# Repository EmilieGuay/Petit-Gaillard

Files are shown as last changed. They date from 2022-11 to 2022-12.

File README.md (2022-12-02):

# Petit Gaillard

Le Petit Gaillard est un robot assez simple à préparer et à programmer. Il possède deux bras qui peuvent bouger grâce à 4 servomoteurs positionnels. 

On peut donc lui faire prendre des postures ou encore le faire danser!

Idéal pour apprendre la programmation des servomoteurs positionnels et aussi très amusant :).

## Programmation

On peut programmer les servomoteurs positionnels pour que leur arbre soit à une position angulaire donnée. Le moteur se positionnera à cet angle et y restera. Les servomoteurs utilisés peuvent généralement couvrir des angles de 0 à 180 degrés. 

Pour des suggestions d'activités à faire avec le Petit Gaillard, voir les documents dans le dossier "Programmation". 

La première activité se nomme "Petit Gaillard", il existe 3 versions, en fonction de l'application utilisée pour programmer le Petit Gaillard, soit mBlock, Blockly ou Arduino IDE. Les feuiles de postures supplémentaires et le défi ultime peuvent être utiles ici. 

Pour une utilisation du Petit Gaillard avec un modèle d'intelligence artificielle (classification d'images, de sons ou de postures), consulter le répertoire "App-IA" (www.github.com/EmilieGuay/App-IA). 

La deuxième activité se nomme "Faire danser le Petit Gaillard".

## Matériel et préparation

### Impression 3D

Les fichiers fournis sont en format ".stl". Il est possible de les ouvrir dans un logiciel d'impression 3D pour les péparer pour l'impression. 
Pour obtenir des formats de fichiers modifiables, contactez-moi. 

À noter : les deux bras sont identiques, de même que les deux avant-bras.

Il est possible que les formes doivent être tournées pour permettre une meilleure impression. Le haut, par exemple, devrait se trouver la face contre la surface d'impression et non pas debout. Pour les bras et les avant-bras, il est mieux de les mettre à plat, avec la face comprenant l'emplacement pour le bras/embout/corne pour le servomoteur vers le haut.

Les pièces n'ont pas besoin d'une grande précision. Généralement, 0.28 mm comme épaisseur de couche devrait convenir, mais il pourrait être utile de choisir plus petit (0.20mm ou 0.16 mm) pour les bras et les avant-bras. Une densité de remplissage autour de 15 % devrait convenir.

Le haut entre directement dans le bas. Les deux pièces devraient s'emboîter assez bien pour ne pas avoir besoin de fixation supplémentaire. Il faut parfois sable un peu le haut pour qu'il soit facile à placer dans le bas

### Version "bricolage à la maison"

Pour ceux qui souhaiteraient faire leur porpre Petit Gaillard, mais qui n'ont pas d'imprimante 3D, il est aussi possible d'en fabriquer un en carton. Pour de meilleurs résultats, utiliser un carte très rigide pour le corps, les bras et les avant-bras. Pour la base du robot, il faudra voir ce qui est disponible à la maison. On peut, par exemple, se servir d'une boîte de céréales vide. Il faudra peut-être renforcer certaines parties. La base de la boîte peut servir de base au robot. et on découpe le coprs et la base d'une seule pièce dans la boîte. 

Il est important que le matériel pour faire les bras et les avant-bras soit léger car les servomoteurs suggérés (format micro) ne sont pas conçus pour lever des grandes charges. 

Le fichier "Dimensions.pdf" peut aider dans la planification, mais c'est aussi une bonne opportunité de laisser aller son imagination.

Pour fixer les servomoteurs et leurs attaches sur le robot, la colle chaude et le ruban adhésif sont assez efficaces. 

### Choix des servomoteurs

Vous devez utiliser des servomoteurs positionnels pour réaliser le Petit Gaillard. Acheter ceux dont les fils se trouvent à la base, et non sur le côté. Sinon, il risque d'être difficile de les installer sur les bras ou le haut du robot. Si on installe les servomoteurs différemment que la méthode proposée, il risque de ne pas y avoir assez d'espace pour que les bras puissent bouger.  Pour plus d'informations, voir le document "Matériel et préparation du Petit Gaillard.pdf". Vous pouvez aussi consulter le vidéo sur le Petit Gaillard. 

De préférence, choisir des servomoteurs qui permettent une alimentation entre 4.8V à 6V.

## Vidéos

à venir

Des activités supplémentaires seront ajoutées avec le temps

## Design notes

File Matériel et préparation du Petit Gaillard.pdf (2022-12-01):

### 1. Introduction

Le Petit Gaillard est un robot simple qui est une bonne introduction à la programmation des robots et à l’utilisation des servomoteurs positionnels. Il possède deux bras qui peuvent bouger grâce à un servomoteur dans l’épaule et un autre dans le coude.

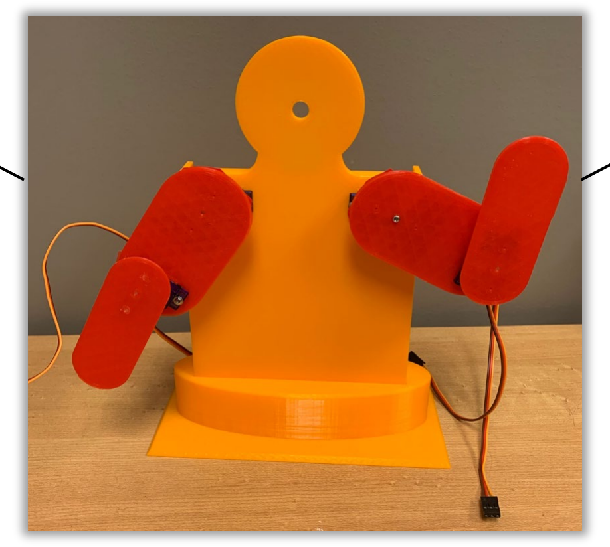
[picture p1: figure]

On peut donc le faire prendre des poses en particulier ou encore le faire danser !

Le présent document présente les pièces formant le Petit Gaillard et la façon de l’assembler au départ.

Attention : dans le présent document et les autres documents préparer, la gauche et la droite du robot sont définie comme sur la figure suivante. Il s’agit de votre gauche ou votre droite, comme si le robot était votre image dans le miroir.

# Matériel d’un kit du Petit Gaillard et préparation

## Club de robotique

### CÉGEP DE JONQUIÈRE

Droite du
robot

Gauche du
robot

2

### 2. Matériel

- 1 carte Arduino
- 1 fils USB-B vers USB-A long
- 4 x 3 fils mâle-mâle
- 4x 3 fils mâle-femelle
- 4 servomoteurs positionnels format micro dont les fils sortent vers le bas du servomoteur et non le côté. De préférence permettant des tensions entre 4.8 V et 6V.
- 1 platine d’essai moyenne

Impression 3D :
- 1 dessous du robot
- 1 corps du robot
- 2 bras
- 2 avant-bras

Alimentation recommandée :
- 1 support de pile 4xAA
- 4 piles AA (peuvent être rechargeables)

Autre alimentation possible :
- 1 blindage Gravity: IO Expansion Shield for Arduino V7.1 de DFRobot

Pour l’installation des servomoteurs :
- 1 petit tournevis cruciforme
- 1 fusil à colle chaude ou ruban adhésif de type électrique

### 3. Assemblage

### Les avant-bras

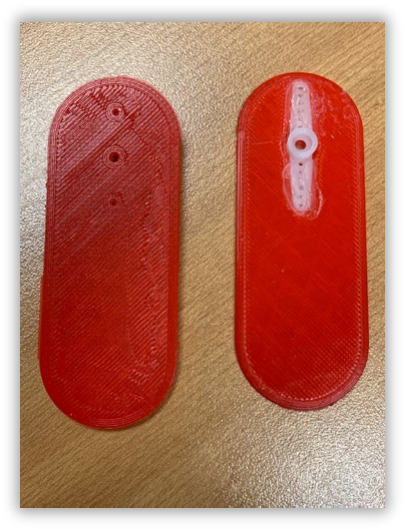
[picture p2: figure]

Les deux avant-bras sont identiques. Il suffit de fixer les attaches pour servomoteurs (en général, elles viennent avec les servomoteurs quand on les achète) dans l’emplacement prévu à cette fin sur la pièce imprimées 3D. On peut la fixer avec de la colle chaude ou autre type de colle (la colle en bâton ne fonctionne pas à cette fin) ou un ruban adhésif électrique (isolant) ou autre. On peut aussi utiliser des petites vis qui sont fournies avec le servomoteur, mais ce n’est pas idéal car elles devraient être utilisées principalement pour fixer les servomoteurs eux-mêmes.

3

Si du ruban adhésif est utilisé, il peut arriver que l’attache du servomoteur se détache de l’avant-bras, mais il faut simplement la fixer à nouveau.

Note : il est possible que l’attache du servomoteur n’entre pas bien dans l’emplacement prévu à cette fin sur l’avant-bras. Le format des attaches varie d’un fabriquant à l’autre, alors il est difficile d’avoir toujours le bon format. Il est toujours possible de modifier l’attache ou de la fixer malgré tout.

### Les bras

Il faut fixer les servomoteurs sur les bras de la façon suivante :

## Bras gauche Bras droit

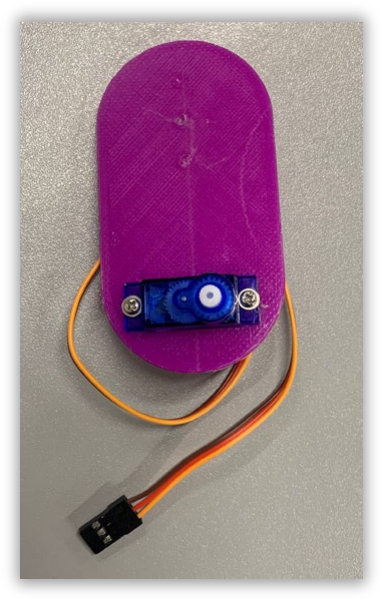
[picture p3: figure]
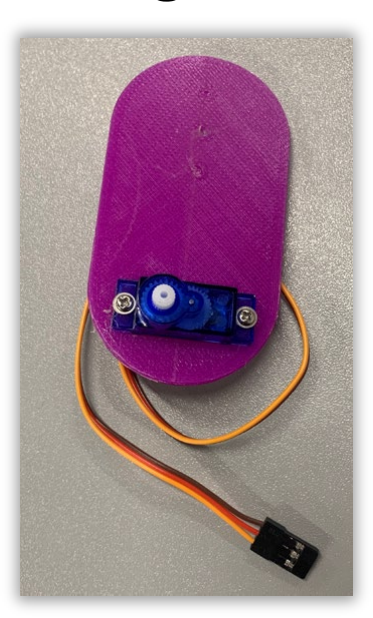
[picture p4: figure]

La face qui est vue ici est la face de devant. Il faut utiliser des vis pour fixer les servomoteurs, ou encore de la colle chaude. Les deux moteurs n’ont pas la même orientation dans les deux cas. Le but est de mettre le fil du servomoteur vers l’extérieur.

Les vis utilisées sont celles qui viennent avec les servomoteurs. Il peut arriver qu’elles dépassent à l’arrière du bras. Il est toujours possible de mettre un peu de colle chaude ou autre chose sur la pointe de la vis qui dépasse pour éviter de se piquer dessus.

Il faut aussi installer une attache pour les servomoteurs sur la face arrière. Procéder comme avec les avant-bras.

La raison pour laquelle il faut absolument que les fils du servomoteur sortent dans le bas de celui-ci est pour pouvoir les installer comme il le faut.

4

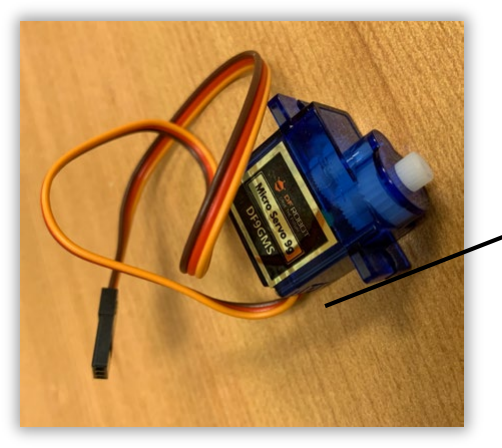
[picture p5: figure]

En effet, si les fils sortent sur le côté, il sera difficile de glisser le servomoteur dans l’ouverture pour qu’il soit ainsi :

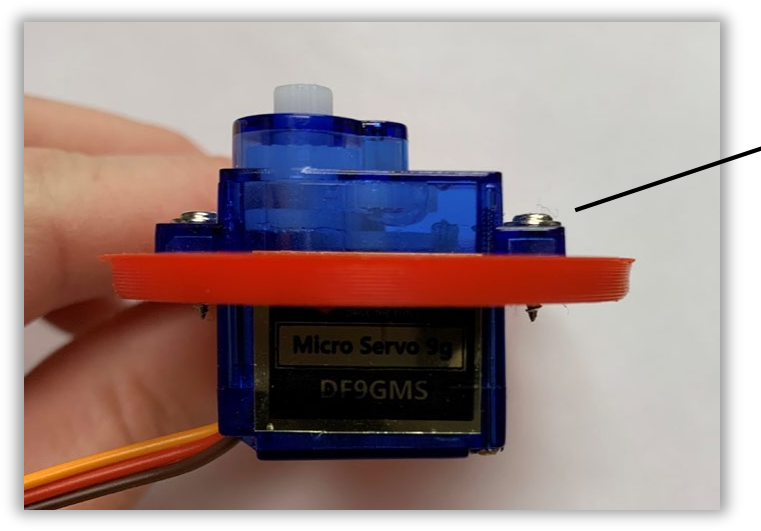
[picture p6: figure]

Sinon, il risque de manquer d’espace pour le que servomoteur du bars puisse passer entre le bras et le corps.

Fil sortant dans
le bas du
servomoteur

Partie plus
large de ce
côté

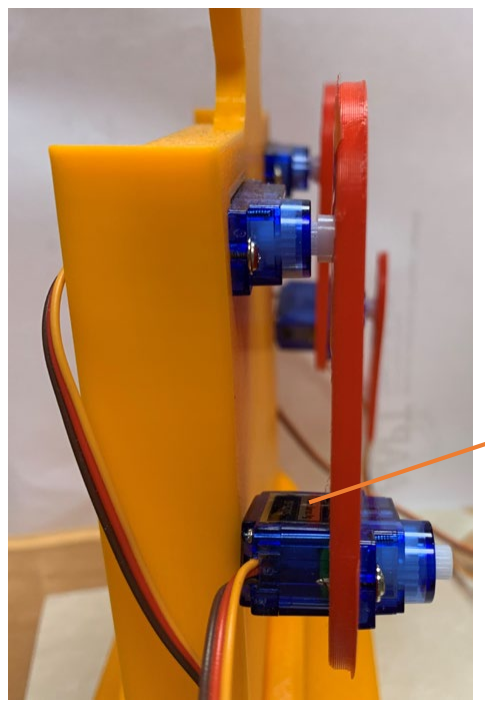
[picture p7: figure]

Espace entre
le bras et le
corps

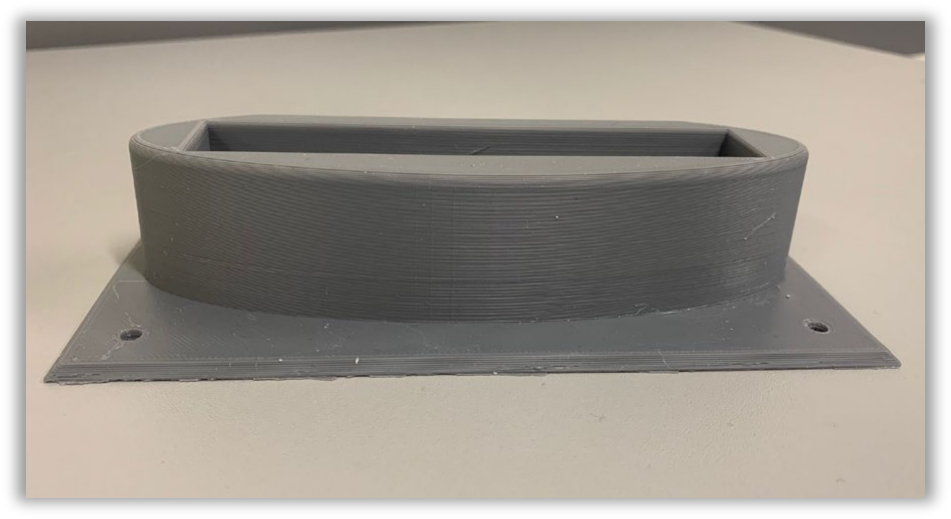
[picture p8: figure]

5

### Le corps du Petit Gaillard

Pour finir la préparation du corps du Petit Gaillard, il suffit de fixer deux servomoteurs dans les ouvertures des épaules. Il faut procéder comme dans le cas des bras, avec la même orientation.

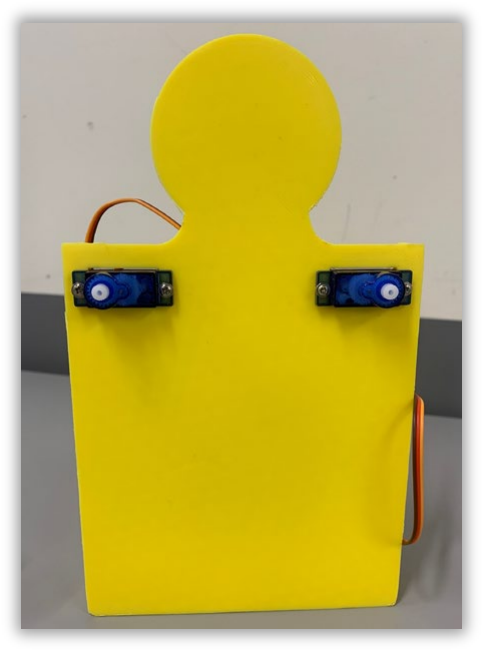
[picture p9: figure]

### Le dessous du Petit Gaillard

Aucune préparation n’est nécessaire !

### Assemblage final :

Placer le corps dans l’ouverture du bas du robot sans autre besoin de fixation. Au besoin, limer un peu la base du corps s’il est difficile de le faire entrer.

Il est préférable de ne pas placer les bras et les avant-bras sur le robot au départ, car on ignore la position des servomoteurs. Pour savoir comment les placer, suivre les instructions du document « Petit Gaillard mBlock.pdf », « Petit Gaillard Blockly.pdf » ou « Petit Gaillard Arduino.pdf ».

### 4. Circuit et alimentation :

Il reste à brancher les servomoteurs dans l’alimentation et la carte Arduino.

Important : Il est mieux les branchements sont faits derrière le Petit Gaillard pour que les fils soient derrière celui-ci.

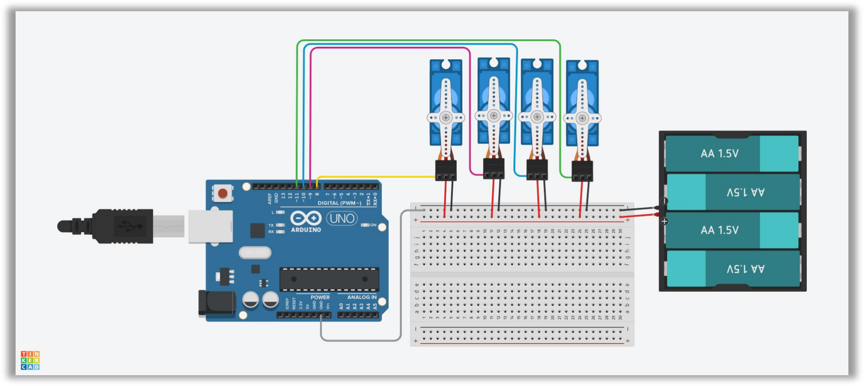
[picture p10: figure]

6

Dans les deux cas, il est recommandé de brancher les fils de signal (fil orange du servomoteur) dans les broches digitales suivantes de la carte Arduino :

Servomoteur | Broche
Épaule Gauche | 8
Épaule Droite | 9
Coude Gauche | 10
Coude Droit | 11

Les autres broches fonctionneraient aussi, mais cela suit ce qui est fait dans les documents d’activités proposées avec le Petit Gaillard. Si on choisit d’autres broches, il faut en tenir compte lors de la programmation.

Alimentation recommandée :

Il est toujours préférable de séparer l’alimentation électrique des moteurs et celle de l’électronique. Parfois, on réussit à le faire avec un circuit, mais on peut aussi utiliser deux sources de courant/tension. Ici, la carte Arduino est alimentée par l’ordinateur via le fil USB et le bloc de 4 piles alimente les servomoteurs.

Il est très important de ne pas oublier de brancher une broche GND de la carte de type Arduino avec la borne négative (« - ») du bloc de piles.

Note : On choisit les piles de telle sorte que l’on respecte la tension recommandée par le fabricant. Certains servomoteurs supportent une tension entre 4.8 V et 6 V, ce qui est parfait avec un bloc de 4 piles AA, rechargeables (4.8 V) ou non (6 V). ON pourrait aussi utiliser des piles AAA si le support de 4 piles utilise ce format.

7

Alimentation alternative 1 :

On peut utiliser la broche +5V comme alimentation pour les servomoteurs. Cependant, il faut s’assurer que les servomoteurs ne restent pas coincés. Ce n’est pas la méthode idéale.

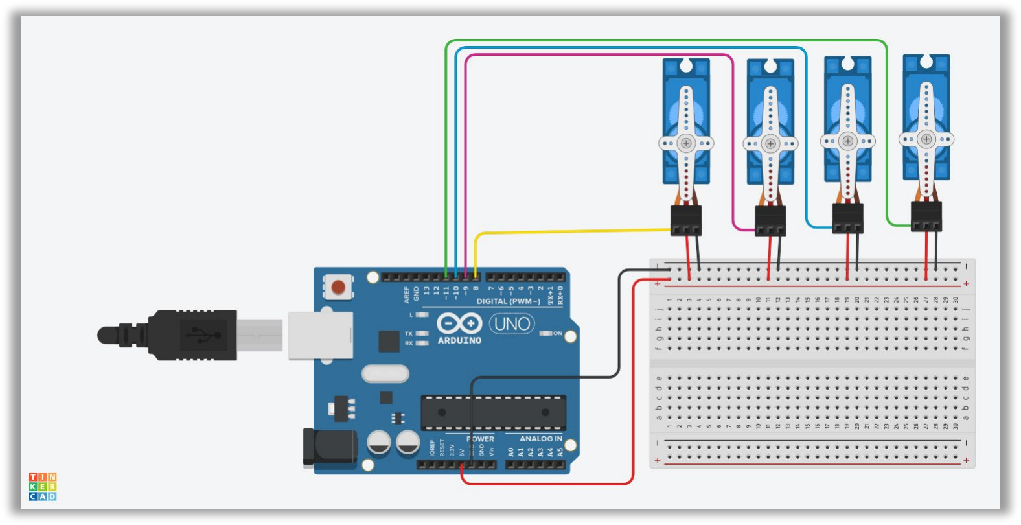
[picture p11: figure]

Il peut arriver que cela demande trop de courant via le port USB et que l’ordinateur déconnecte la carte Arduino.

Autre version alternative

On peut aussi utiliser un blindage (« Shield »), par exemple le Gravity: IO Expansion Shield for Arduino V7.1 de DFRobot.

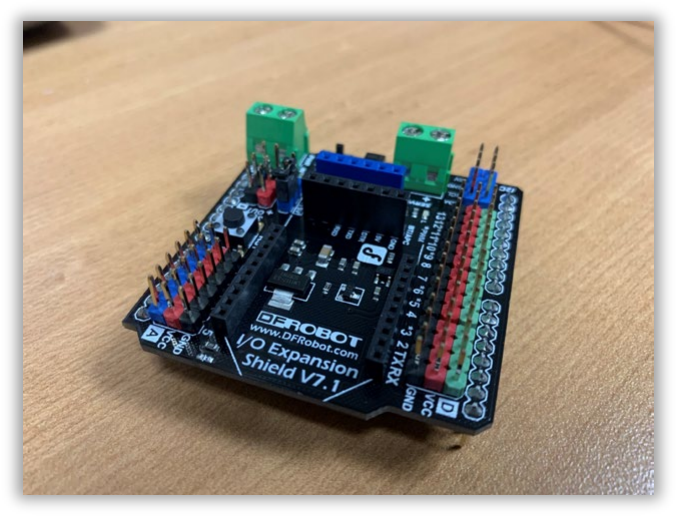
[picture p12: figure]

8

Un blindage est une carte faite spécifiquement pour se brancher par-dessus la carte Arduino.

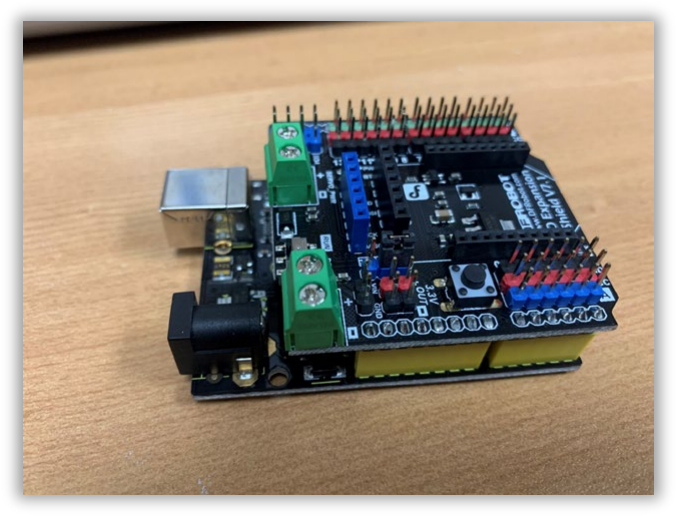
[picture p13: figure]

Il en existe de nombreuses versions qui permettent d’étendre les capacités des cartes de type Arduino dans requérir de branchements complexes. Ici, on peut brancher les servomoteurs directement sur le blindage, comme suit :

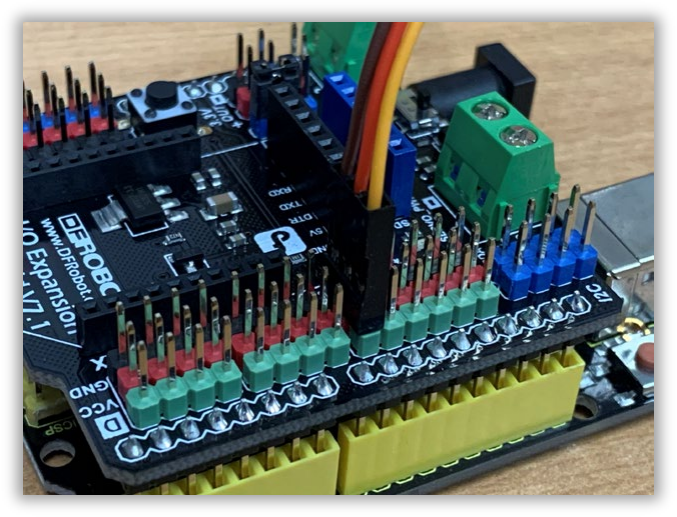
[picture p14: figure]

Il est important que le fil orange du servomoteur (signal) soit branché dans la borne verte, le fil rouge dans la borne rouge et le fil noir dans la borne noire.

Il est à noter ici que la tension est fournie par la borne +5V de la carte Arduino, ce qui revient au même que la version précédente d’alimentation. Cependant, les branchements sont beaucoup plus faciles.

Il est possible d’utiliser une source externe pour la tension fournie sur les bornes rouges du blindage, mais la tension de cette source externe doit être supérieure à 7V pour que cela fonctionne, et c’est trop pour les servomoteurs utilisés. Pour plus d’informations sur ce blindage, voir les ressources du fabricant, DFRobot.

D’autres blindages pourraient peut-être faire le même travail.

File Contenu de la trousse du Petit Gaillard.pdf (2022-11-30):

1

### Contenu de la trousse

- 20 kits du Petit Gaillard (1 à 20)
- 10 clés USB (1 à 10)
- 1 trousse de dépannage
- 20 kits de feuilles avec les formes de couleurs (tm feuilles.docx)

### Contenu d’un kit du Petit Gaillard

- 1 carte Arduino
- 1 blindage d’expansion DFRobot
- 1 platine d’essai moyenne
- 1 fils USB-B vers USB-A long
- 4 x 3 fils mâle-mâle
- 4x 3 fils mâle-femelle
- 1x2 fils mâle-mâle + pince
- 1 petit sac refermable contenant deux attaches supplémentaires
- Les pièces précédentes sont dans une petite boîte 4 po x 3 po x 2 po
- 1 dessous du robot
- 1 corps du robot + 2 servomoteurs positionnels
- 1 bras gauche + servomoteur positionnel
- 1 bras droit + servomoteur positionnel
- 2 avant-bras
- 1 support de pile 4xAA
- Le tout dans une boîte de 8 po x 6 po x 4 po

### Contenu des Clés USB

- Dossier Adar : Fichiers de programmation + Application d’acquisition de données avec Arduino
- Dossier App-IA : Application d’intelligence artificielle, modèle de secours, Logo1.png, Logo gris.png et fichiers de programmation

### Trousse de dépannage

- 6 servomoteurs positionnels supplémentaires + quincaillerie
- 2 petits tournevis

### Liste de matériel Trousse du Petit Gaillard

## Club de robotique

### CÉGEP DE JONQUIÈRE

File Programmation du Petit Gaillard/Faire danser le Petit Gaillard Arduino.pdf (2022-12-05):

### 1. Objectifs :

1. Faire danser le Petit Gaillard en le faisant passer d’une posture à l’autre
2. Utiliser des fonctions pour aider la programmation
3. Faire des mouvements plus graduels en utilisant une boucle « for »

### 2. Matériel :

- Un kit de Petit Gaillard
- Un ordinateur

### 3. Passer d’une posture à l’autre

Préalable :

- Faire les activités du document « Petit Gaillard Arduino.pdf » avant celui-ci.
- Préparer le Petit Gaillard tel que montré dans « Petit Gaillard Arduino.pdf »
- Choisir les postures qui doivent être utilisées dans la danse !

Pour faire danser le Petit Gaillard, la première solution est de le faire passer directement d’une posture à l’autre, en ajoutant un temps d’attente entre les deux. Le but du temps d’attente est simplement pour permettre aux servomoteurs de se rendre à la nouvelle position. Cela peut permettre aussi de synchroniser des mouvements avec un rythme en particulier.

Le premier code proposé permet de faire passer le Petit Gaillard, préalablement préparé avec la méthode proposée dans « Petit Gaillard Arduino.pdf » d’une position où les bras sont complètement en haut à une posture dont les bras sont en coin à 90 degrés.

# Faire danser le Petit Gaillard- Arduino

## Club de robotique

### CÉGEP DE JONQUIÈRE

2

#include <Servo.h>

//Définition des variables moteurs. Servo epauleG;
Servo epauleD;
Servo coudeG;
Servo coudeD;

//Ce code est exécuté une seule fois. void setup() {

epauleG.attach(8);
epauleD.attach(9);
coudeG.attach(10);
coudeD.attach(11);

//Bras en haut
epauleG.write(0);
epauleD.write(180);
coudeG.write(180);
coudeG.write(0);

delay(1000);

//Bras en coin
epauleG.write(90);
epauleD.write(90);
coudeG.write(90);
coudeG.write(90);

delay(1000);
}

//Ce code est exécuté en boucle ensuite.
void loop() {

}

Il y a un temps d’attente de 1 seconde (1000 millisecondes) entre les deux postures.

Ces deux postures ne sont effectuées qu’une seule fois. Pour recommencer le mouvement, il faut couper l’alimentation de la carte Arduino en la débranchant de l’ordinateur et ensuite en la rebranchant. On peut aussi tout simplement appuyer sur le bouton « reset » qui se trouve sur la carte Arduino.

3

Si on veut programmer un mouvement qui se répète, on doit mettre les lignes de code contrôlant les servomoteurs et le temps d’attente dans la fonction « loop », comme ceci :

#include <Servo.h>

//Définition des variables moteurs.
Servo epauleG;
Servo epauleD;
Servo coudeG;
Servo coudeD;

//Ce code est exécuté une seule fois. void setup() {
epauleG.attach(8);
epauleD.attach(9);
coudeG.attach(10);
coudeD.attach(11);
}

//Ce code est exécuté en boucle ensuite. void loop() {

//Bras en haut
epauleG.write(0);
epauleD.write(180);
coudeG.write(180);
coudeG.write(0);

delay(1000);

//Bras en coin
epauleG.write(90);
epauleD.write(90);
coudeG.write(90);
coudeG.write(90);

delay(1000);

}

Tout ce qui est placé dans la fonction « loop » sera effectué pour toujours. Donc, une fois que les lignes de code à l’intérieur ont été exécutées, on recommence au début de la fonction « loop ». Le tout sera exécuté tant que la carte Arduino est alimentée.

4

Il n’est pas toujours nécessaire d’avoir un bloc de contrôle pour la position de chaque servomoteur, si, par exemple, un moteur reste à la même position entre deux postures.

Défi : créer une danse avec au moins 4 postures différentes et des temps d’attente qui varient entre les 4 postures. On peut mettre plus de postures, bien sûr…

### 4. Utilisation des fonctions

On remarque assez vite que le code permettant de faire une danse devient très long rapidement et qu’il est parfois difficile de se rappeler l’ordre de chaque posture. En plus, si l’on utilise plusieurs fois la même posture, on répète exactement les mêmes lignes de code.

Pour faciliter la lecture, la programmation et aussi pour éviter que des sections de code ne se répètent, on peut utiliser des fonctions. Celles-ci permettent de regrouper une partie de code et de le réutiliser à plusieurs endroits dans le code.

Par exemple, nous créerons une fonction pour la posture des bras en coin. On place les définitions des fonctions en-dessous de la boucle « loop », après la fermeture de son accolade. En fait, on pourrait placer les fonctions n’importe où dans le code, soit avant la fonction « setup », entre les fonctions « setup » et « loop » ou après celle-ci. C’est un choix. Pour l’instant, elles seront placées en-dessous de « loop ». On peut donc modifier le code comme ceci :

#include <Servo.h>

//Définition des variables moteurs.
Servo epauleG;
Servo epauleD;
Servo coudeG;
Servo coudeD;

//Ce code est exécuté une seule fois.
void setup() {

//Il faudra peut-être changer la valeur de la broche pour //les moteurs
epauleG.attach(8);
epauleD.attach(9);
coudeG.attach(10);
coudeD.attach(11);
}

5

//Ce code est exécuté en boucle ensuite. void loop() {

//Bras en haut
epauleG.write(0);
epauleD.write(180);
coudeG.write(180);
coudeG.write(0);
delay(1000);

//Bras en coin
brasEnCoin(); //Utilisation de la fonction brasEnCoin() delay(1000);
}

//Ceci est une fonction. Ici, ce n'est que la définition. void brasEnCoin() {
epauleG.write(90);
epauleD.write(90);
coudeG.write(90);
coudeG.write(90);
}

Pour utiliser la fonction, on doit l’utiliser dans « loop » ou « setup ».

Défi : Créer une fonction pour chaque posture déjà utilisée précédemment et les utiliser dans « loop ».

On peut aussi créer des fonctions qui prennent une valeur en entrée. Par exemple, on pourrait créer une fonction appelée « posture » qui prend 4 valeurs numériques (entiers ou « int ») en entrée, appelées angle1, angle2, angle3 et angle4.

void posture (int angle1, int angle2, int angle3, int angle4) {

epauleG.write(angle1);
epauleD.write(angle2);
coudeG.write(angle3);
coudeG.write(angle4);

}

6

Lorsqu’on utilise cette fonction, il faut entrer 4 valeurs numériques (entiers) à l’intérieur de la parenthèse (le reste du code a omis ici, mais doit être présent pour que le code fonctionne):

void loop() {

//Bras en haut
posture(0, 180, 180, 0);
delay(1000);

//Bras en coin
posture(90, 90, 90, 90); //Utilisation de la fonction delay(1000);
}

void posture (int angle1, int angle2, int angle3, int angle4) {

epauleG.write(angle1);
epauleD.write(angle2);
coudeG.write(angle3);
coudeG.write(angle4);
}

Défi : Créer une fonction « posture2 » qui prend en entrée 4 valeurs d’angle et un temps d’attente et l’utiliser pour créer une danse.

### 5. Utilisation des boucles « for »

Supposons que l’on souhaite répéter une action pour toujours, on peut utiliser le bloc « loop ». Cependant, il existe d’autres structures de contrôle qui permettent de répéter une série de lignes de code pour un nombre de fois prédéterminé où jusqu’à ce qu’une certaine condition soit atteinte.

Regardons les boucles « for » :

for(int i =0 ; condition ; i = i +increment){
//code à exécuter
}

La fonction for (« pour » en français) est une fonction très importante et très utilisée pour réaliser des boucles de contrôle dans un programme.

7

Elle a trois arguments :
1. Le premier est la valeur d’initialisation. Ici, on déclare la variable i qui n’existera donc que dans la boucle for. On lui attribue sa valeur de départ dans la boucle. C’est la valeur de la variable i au premier passage dans la boucle.
2. Le deuxième argument est la condition. La boucle sera exécutée tant que la condition est vraie. Si la condition devient fausse, on sort de la boucle et on passe aux commandes suivantes.
3. Le troisième argument est appelé l’incrément. Il indique comment la variable i sera modifiée à chaque exécution du bloc d’instructions de la boucle. L’incrément peut être fait avec une soustraction, une multiplication ou une division.
Par exemple:

for(int i =0 ; i < 3 ; i = i + 1){
//code à exécuter
}

Le déroulement de l’exécution de la boucle sera ainsi : Début de la boucle :
1er passage :
i=0
la condition est vraie, on exécute le bloc de commandes i=0+1 =1
2e passage :
i=1
La condition est vraie, on exécute le bloc de commandes i=1+1=2
3e passage :
i=2
La condition est vraie, on exécute le bloc de commandes i=2+1=3
4e passage
i=3
La condition est fausse, on n’exécute pas le bloc de commandes et on sort de la boucle for.
Fin de la boucle

Il est possible d’utiliser une autre valeur de départ que 0, de changer la condition pour autre chose et aussi de changer la valeur de l’incrément. Ici, on a utilisé une valeur de « 1 ». Cela fait faire des bonds de 1 à la valeur de « i », mais on pourrait aussi utiliser des valeurs plus grandes, 2, 3, 4, etc. On pourrait aussi utiliser des valeurs négatives, ce qui ferait diminuer la valeur de i.

Défi : Utiliser un boucle « for » pour refaire 3 fois le même changement entre 2 postures différentes. Utiliser les fonctions créées plus haut pour faire les postures.

8

On peut aussi utiliser la valeur de « i » pour contrôler l’angle d’un servomoteur. Ainsi, on peut rendre un mouvement plus graduel ou pour en contrôler le rythme. Jusqu’ici, le passage entre deux postures s’effectue très rapidement. Si l’on souhaite plutôt que le passage d’un bras d’en bas à en haut se fasse en un temps plus long, on ne peut pas simplement passer de la position du bras en haut à en bas directement, car le mouvement se fait tout d’un coup. Il faut plutôt passer par plusieurs valeurs d’angle intermédiaires et mettre un temps d’attente entre chaque valeur.

Par exemple si on veut qu’un moteur passe d’un angle de 0 degré à un angle de 180 degrés en environ 1 seconde, on pourrait lui faire faire des bonds de 10 degrés à chaque 0.05 secondes. Bien entendu, programmer au long chaque changement serait très long… Avec une boucle « for », cela revient à :

for(int angle=0 ; angle <= 180 ; angle = angle + 10){ epauleG.write(angle);
delay(50);
}

On peut ajuster le mouvement en modifiant le temps d’attente, les angles de départ et d’arrivée et de de combien on modifie la valeur de l’angle d’un passage à l’autre dans la boucle. Si l’on fait des bonds de plus grande valeur, le mouvement sera plus saccadé. Même chose si l’on augmente la valeur de temps d’attente entre deux valeurs. En revanche, le mouvement sera plus rapide si le temps d’attente est plus court et si les bonds sont plus grands. Il faut donc trouver la meilleure combinaison entre la rapidité et la fluidité.

Défi : Faire tourner les deux avant-bras en même temps en un mouvement lent et graduel pour passer d’une posture à l’autre comme ceci :

### 6. Défi ultime

Choisir une chanson de votre choix et synchroniser les mouvements du Petit Gaillard avec la musique ! Utiliser les postures choisies ou d’autres, des blocs « Répéter x fois », des blocs « Répéter jusqu’à » et des blocs personnalisés !

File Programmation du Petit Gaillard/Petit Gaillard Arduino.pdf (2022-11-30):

### Objectifs :

- Préparer le Petit Gaillard pour son utilisation
- Programmer le Petit Gaillard pour faire différentes postures et mouvements

### Matériel :

- Morceaux de Petit Gaillard (1 corps, 1 support, 2 bras, 2 avant-bras)
- 4 micro-servomoteurs positionnels+ attaches
- Fils
- Carte Arduino Uno +fil USB
- Fil d’alimentation 12 V ou bloc-piles + piles
- Ordinateur
- Platine d’essai

### Déroulement :

- Monter le robot sur sa base
- Positionner les moteurs et attacher les bras et les avant-bras sur le robot
- Programmer le robot pour différents mouvements de danse

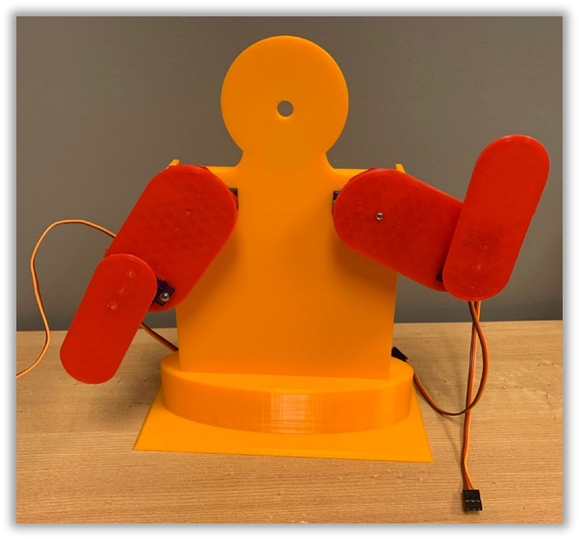
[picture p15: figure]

### Le Petit Gaillard

# Le Petit Gaillard (mBlock)

## Club de robotique

### CÉGEP DE JONQUIÈRE

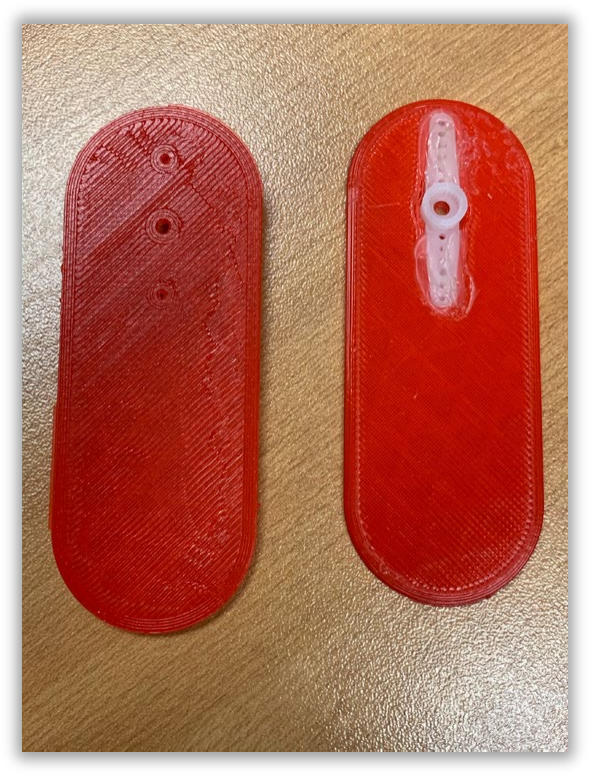
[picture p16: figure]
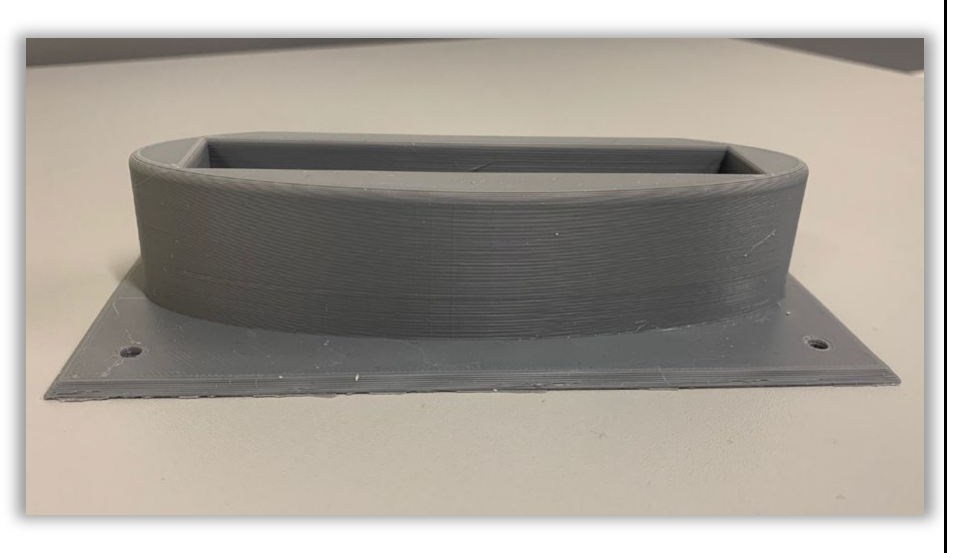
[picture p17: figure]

2

Le principe de base du Petit Gaillard est assez simple. Quatre servomoteursservent à faire bouger les bras. Chaque servomoteur permet une rotation de son arbre de 180 degrés. Il y a un moteur pour chaque coude et un moteur pour chaque épaule.

En programmant la position des servomoteurs, on peut faire bouger les bras du robot.

### Parties du robot :

Bras gauche | Bras droit | Avant-bras (2)

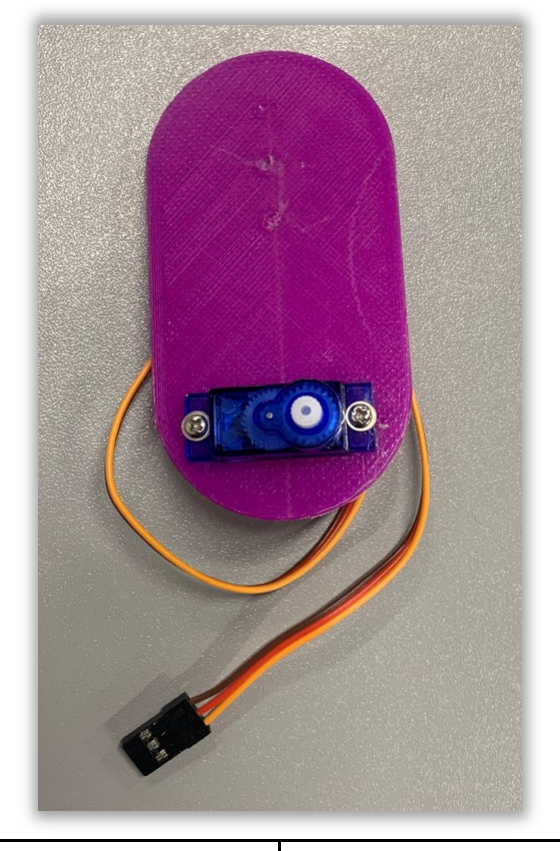
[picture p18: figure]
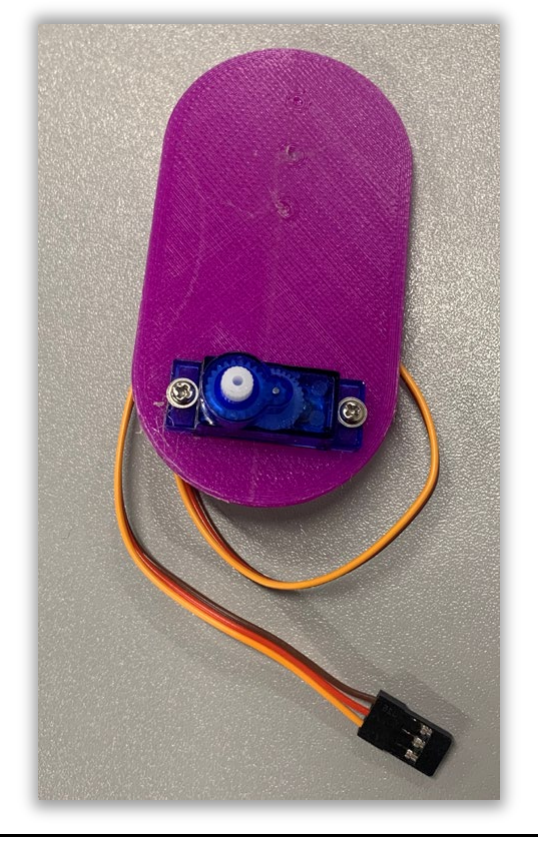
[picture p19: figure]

Corps | Dessous

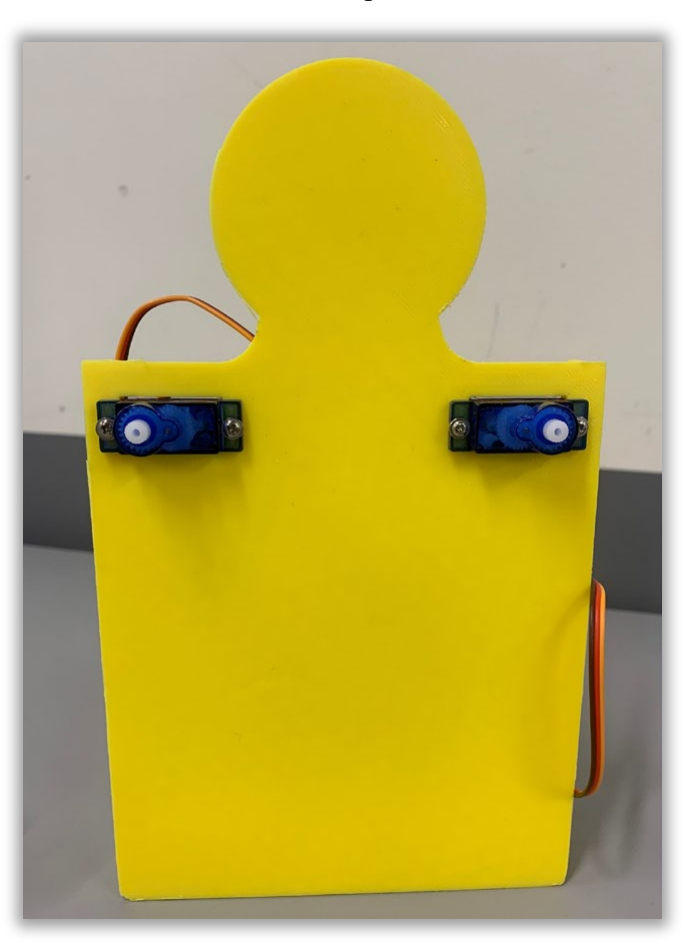
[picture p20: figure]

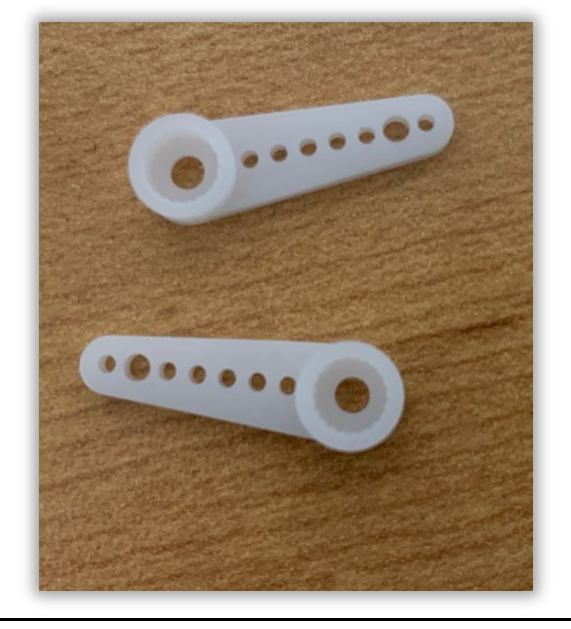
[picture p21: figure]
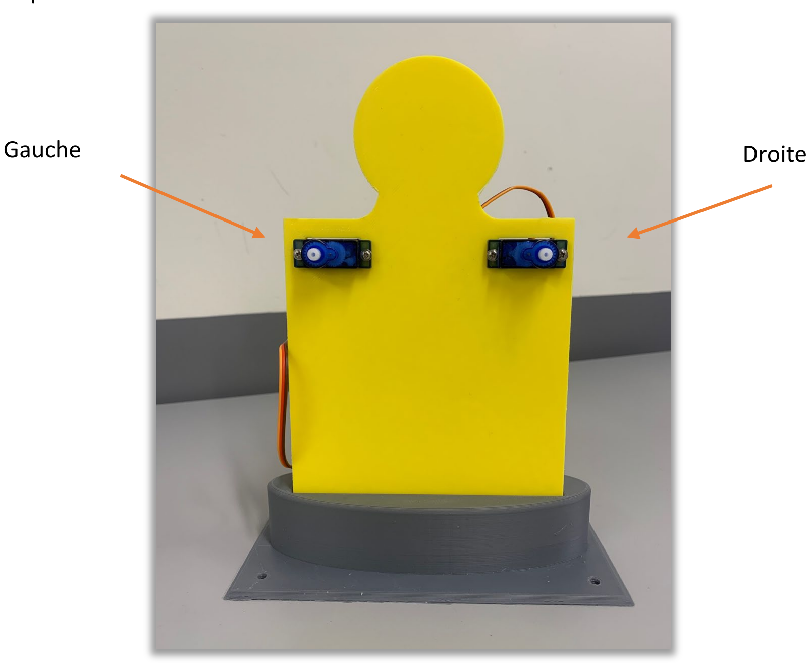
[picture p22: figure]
Gauche; Droite

3

## Servomoteurs (4 déjà installés) Attaches supplémentaires (2)

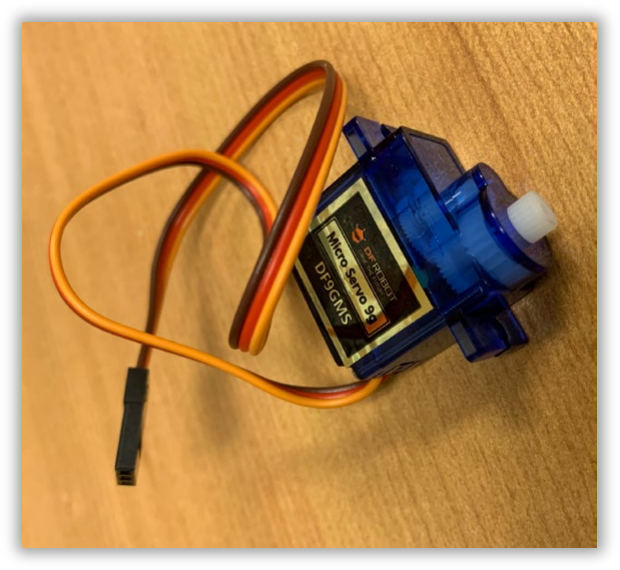
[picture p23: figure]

### Préparation

1. La première étape consiste à placer le corps et dans le support pour que le robot se tienne debout. Les deux servomoteurs des épaules sont déjà en place sur le corps. On obtient ceci :

Dans le présent document, la gauche du robot est votre gauche et non la sienne.

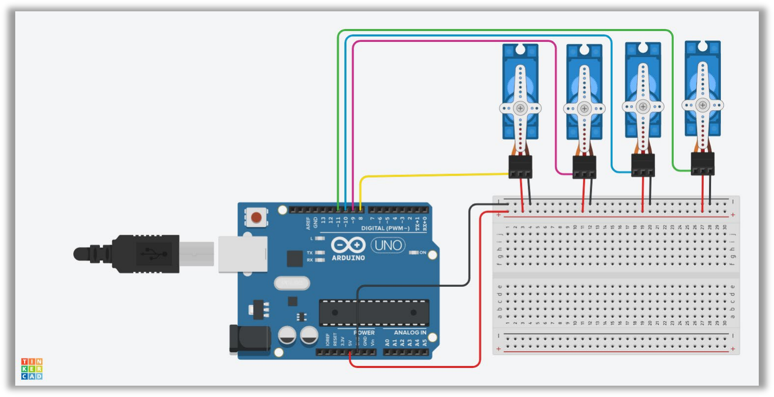
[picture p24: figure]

4

2. Brancher les servomoteurs comme suit :

Le tableau suivant vous indique quel moteur brancher dans quelle broche digitale de la carte Arduino :

Servomoteur | Broche
Épaule Gauche | 8
Épaule Droite | 9
Coude Gauche | 10
Coude Droit | 11

Pour brancher les servomoteurs, il faut noter que le fil rouge doit aller sur la broche +5V, le fil noir ou brun sur la broche GND et le fil orange ou jaune sur la broche digitale qui contrôle le moteur en question.

Petit truc :

Bien s’assurer que les fils passent derrière le robot et que la carte Arduino aussi est derrière le robot. Cela évitera que les fils n’entravent le mouvement des bras.

5

3. Dans Arduino, écrire le code suivant : #include <Servo.h>

Servo epauleGauche;
Servo epauleDroite;
Servo coudeGauche;
Servo coudeDroit;

void setup(){
epauleGauche.attach(8);
epauleDroite.attach(9);
coudeGauche.attach(10);
coudeDroit.attach(11);
}

void loop(){
epauleGauche.write(180);
epauleDroite.write(0);
coudeGauche.write(180);
coudeDroit.write(0);
}
4. Téléverser ensuite le code dans la carte Arduino.
5. Une fois que les moteurs sont immobiles (ça devrait être assez rapide), placer d’abord les bras et ensuite les avant-bras pour obtenir la posture suivante :


6. À la suite du code précédent, ajouter les blocs nécessaires pour obtenir le code suivant et le téléverser dans la carte.
7.

6

#include <Servo.h>

Servo epauleGauche;
Servo epauleDroite;
Servo coudeGauche;
Servo coudeDroit;

void setup(){
epauleGauche.attach(8);
epauleDroite.attach(9);
coudeGauche.attach(10);
coudeDroit.attach(11);
}

void loop(){
epauleGauche.write(180);
epauleDroite.write(0);
coudeGauche.write(180);
coudeDroit.write(0);

delay(1000);

epauleGauche.write(0);
epauleDroite.write(180);
coudeGauche.write(180);
coudeDroit.write(0);

}

Les deux bras devraient passer de la position complètement en bas à la position complètement en haut, en tournant vers l’extérieur, comme suit :


Sinon, vérifier les branchements, enlever les bras et les avant-bras du robot et recommencer à l’étape 3.


8. À partir du programme précédent, faire un programme pour reproduire chacune
des postures suivantes du robot. Noter aussi les valeurs des angles qui
correspondent :


8

9. Inventez vos propres postures et inscrire les angles qui correspondent :


10. En modifiant le code utilisé pour l’App-IA avec les 3 DEL, programmer le robot pour 3 postures différentes au choix lorsque l’App-IA reconnaîtra les couleurs Bleu, Rouge ou Vert.

Défi ultime :

Faire un autre modèle d’IA permettant de reconnaître 4 classes d’images ou plus et l’entraîner. Programmer le robot pour qu’il ait une posture différente pour chacune de ces postures.

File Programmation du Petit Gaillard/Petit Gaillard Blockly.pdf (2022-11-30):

### Objectifs :

- Préparer le Petit Gaillard pour son utilisation
- Programmer le Petit Gaillard pour faire différentes postures et mouvements

### Matériel :

- Morceaux de Petit Gaillard (1 corps, 1 support, 2 bras, 2 avant-bras)
- 4 micro-servomoteurs positionnels+ attaches
- Fils
- Carte Arduino Uno +fil USB
- Fil d’alimentation 12 V ou bloc-piles + piles
- Ordinateur
- Platine d’essai

### Déroulement :

- Monter le robot sur sa base
- Positionner les moteurs et attacher les bras et les avant-bras sur le robot
- Programmer le robot pour différents mouvements de danse


### Le Petit Gaillard

# Le Petit Gaillard (Blockly)

## Club de robotique

### CÉGEP DE JONQUIÈRE


2

Le principe de base du Petit Gaillard est assez simple. Quatre servomoteursservent à faire bouger les bras. Chaque servomoteur permet une rotation de son arbre de 180 degrés. Il y a un moteur pour chaque coude et un moteur pour chaque épaule.

En programmant la position des servomoteurs, on peut faire bouger les bras du robot.

### Parties du robot :

Bras gauche | Bras droit | Avant-bras (2)


Corps | Dessous


Gauche; Droite

3

## Servomoteurs (4 déjà installés) Attaches supplémentaires (2)


### Préparation

1. La première étape consiste à placer le corps et dans le support pour que le robot se tienne debout. Les deux servomoteurs des épaules sont déjà en place sur le corps. On obtient ceci :

Dans le présent document, la gauche du robot est votre gauche et non la sienne.


4

2. Brancher les servomoteurs comme suit :

Le tableau suivant vous indique quel moteur brancher dans quelle broche digitale de la carte Arduino :

Servomoteur | Broche
Épaule Gauche | 8
Épaule Droite | 9
Coude Gauche | 10
Coude Droit | 11

Pour brancher les servomoteurs, il faut noter que le fil rouge doit aller sur la broche +5V, le fil noir ou brun sur la broche GND et le fil orange ou jaune sur la broche digitale qui contrôle le moteur en question.

Petit truc :

Bien s’assurer que les fils passent derrière le robot et que la carte Arduino aussi est derrière le robot. Cela évitera que les fils n’entravent le mouvement des bras.

3. On veut ensuite mettre les 4 servomoteurs aux valeurs d’angle qui permettront d’obtenir les deux bras et avant-bras en bas. Ensuite, il sera possible d’installer, sans les forcer, les bras et les avant-bras. Pour les bras, il faut s’assurer de mettre le bras gauche à gauche et le bras droit à droite…

5

4. Ouvrir Blockly avec le lien fourni par l’enseignant(e) et suivre les étapes suivantes pour créer le code :

Il faut utiliser un bloc « attacher un servomoteur » pour chaque moteur et utilisé le numéro de la broche dans laquelle ce moteur est branché. De plus, chaque servomoteur doit avoir un identifiant (nom) différent.

Pour modifier l’identifiant d’un servomoteur
- Placer un nouveau bloc « attacher un servomoteur »
- Cliquer sur la liste déroulante située à côté de « avec pour identifiant » :
- Choisir « Renommer cette instance » dans la liste déroulante.
- Inscrire un nouveau nom, sans accent et SANS ESPACE

Il peut être pratique de donner des noms significatifs aux servomoteurs. Par exemple, pour les deux servomoteurs des épaules :


Il sera possible, par la suite, d’utiliser ces identifiants dans les blocs de la section servomoteurs :

Ne pas
mettre
d’espace
entre les
mots


6


Reproduire le code suivant :

Ne pas
mettre
d’espace
entre les
mots

7

5. Copier le code et le coller dans Arduino IDE. Téléverser ensuite le code dans la carte Arduino.
6. Une fois que les moteurs sont immobiles (ça devrait être assez rapide), placer d’abord les bras et ensuite les avant-bras pour obtenir la posture suivante :


7. À la suite du code précédent, ajouter les blocs suivants, copier-coller le code dans Arduino IDE et le téléverser dans la carte.


Les deux bras devraient passer de la position complètement en bas à la position
complètement en haut, en tournant vers l’extérieur, comme suit :

8. À partir du programme précédent, faire un programme pour reproduire chacune
des postures suivantes du robot. Noter aussi les valeurs des angles qui
correspondent :


9


9. Inventez vos propres postures et inscrire les angles qui correspondent :


10. En modifiant le code utilisé pour l’App-IA avec les 3 DEL, programmer le robot pour 3 postures différentes au choix lorsque l’App-IA reconnaîtra les couleurs Bleu, Rouge ou Vert.

Défi ultime :

Faire un autre modèle d’IA permettant de reconnaître 4 classes d’images ou plus et l’entraîner. Programmer le robot pour qu’il ait une posture différente pour chacune de ces postures.

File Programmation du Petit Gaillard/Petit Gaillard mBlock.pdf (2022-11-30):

### Objectifs :

- Préparer le Petit Gaillard pour son utilisation
- Programmer le Petit Gaillard pour faire différentes postures et mouvements

### Matériel :

- Morceaux de Petit Gaillard (1 corps, 1 support, 2 bras, 2 avant-bras)
- 4 micro-servomoteurs positionnels+ attaches
- Fils
- Carte Arduino Uno +fil USB
- Fil d’alimentation 12 V ou bloc-piles + piles
- Ordinateur
- Platine d’essai

### Déroulement :

- Monter le robot sur sa base
- Positionner les moteurs et attacher les bras et les avant-bras sur le robot
- Programmer le robot pour différents mouvements de danse


### Le Petit Gaillard

# Le Petit Gaillard (mBlock)

## Club de robotique

### CÉGEP DE JONQUIÈRE


2

Le principe de base du Petit Gaillard est assez simple. Quatre servomoteursservent à faire bouger les bras. Chaque servomoteur permet une rotation de son arbre de 180 degrés. Il y a un moteur pour chaque coude et un moteur pour chaque épaule.

En programmant la position des servomoteurs, on peut faire bouger les bras du robot.

### Parties du robot :

Bras gauche | Bras droit | Avant-bras (2)


Corps | Dessous


Gauche; Droite

3

## Servomoteurs (4 déjà installés) Attaches supplémentaires (2)


### Préparation

1. La première étape consiste à placer le corps et dans le support pour que le robot se tienne debout. Les deux servomoteurs des épaules sont déjà en place sur le corps. On obtient ceci :

Dans le présent document, la gauche du robot est votre gauche et non la sienne.


4

2. Brancher les servomoteurs comme suit :

Le tableau suivant vous indique quel moteur brancher dans quelle broche digitale de la carte Arduino :

Servomoteur | Broche
Épaule Gauche | 8
Épaule Droite | 9
Coude Gauche | 10
Coude Droit | 11

Pour brancher les servomoteurs, il faut noter que le fil rouge doit aller sur la broche +5V, le fil noir ou brun sur la broche GND et le fil orange ou jaune sur la broche digitale qui contrôle le moteur en question.

Petit truc :

Bien s’assurer que les fils passent derrière le robot et que la carte Arduino aussi est derrière le robot. Cela évitera que les fils n’entravent le mouvement des bras.

5

3. Dans mBlock, écrire le code suivant :


4. Téléverser ensuite le code dans la carte Arduino.
5. Une fois que les moteurs sont immobiles (ça devrait être assez rapide), placer d’abord les bras et ensuite les avant-bras pour obtenir la posture suivante :


6. À la suite du code précédent, ajouter les blocs nécessaires pour obtenir le code suivant et le téléverser dans la carte.

6


Les deux bras devraient passer de la position complètement en bas à la position complètement en haut, en tournant vers l’extérieur, comme suit :


Sinon, vérifier les branchements, enlever les bras et les avant-bras du robot et recommencer à l’étape 3.


7. À partir du programme précédent, faire un programme pour reproduire chacune
des postures suivantes du robot. Noter aussi les valeurs des angles qui
correspondent :


8

8. Inventez vos propres postures et inscrire les angles qui correspondent :


9. En modifiant le code utilisé pour l’App-IA avec les 3 DEL, programmer le robot pour 3 postures différentes au choix lorsque l’App-IA reconnaîtra les couleurs Bleu, Rouge ou Vert.

Défi ultime :

Faire un autre modèle d’IA permettant de reconnaître 4 classes d’images ou plus et l’entraîner. Programmer le robot pour qu’il ait une posture différente pour chacune de ces postures.

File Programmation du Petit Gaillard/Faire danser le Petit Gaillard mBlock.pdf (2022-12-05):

### 1. Objectifs :

1. Faire danser le Petit Gaillard en le faisant passer d’une posture à l’autre
2. Utiliser des blocs personnalisés pour aider la programmation
3. Faire des mouvements plus graduels en utilisant un bloc « répéter »

### 2. Matériel :

- Un kit de Petit Gaillard
- Un ordinateur

### 3. Passer d’une posture à l’autre

Préalable :

- Faire les activités du document « Petit Gaillard mBlock.pdf » avant celui-ci.
- Préparer le Petit Gaillard tel que montré dans « Petit Gaillard mBlock.pdf »
- Choisir les postures qui doivent être utilisées dans la danse !

Pour faire danser le Petit Gaillard, la première solution est de le faire passer directement d’une posture à l’autre, en ajoutant un temps d’attente entre les deux. Le but du temps d’attente est simplement pour permettre aux servomoteurs de se rendre à la nouvelle position. Cela peut permettre aussi de synchroniser des mouvements avec un rythme en particulier.

Le premier code proposé permet de faire passer le Petit Gaillard, préalablement préparé avec la méthode proposée dans « Petit Gaillard mBlock.pdf » d’une position où les bras sont complètement en haut à une posture dont les bras sont en coin à 90 degrés.

# Faire danser le Petit Gaillard- mBlock

## Club de robotique

### CÉGEP DE JONQUIÈRE

2


Il y a un temps d’attente de 1 seconde entre les deux postures.

Ces deux postures ne sont effectuées qu’une seule fois. Pour recommencer le mouvement, il faut couper l’alimentation de la carte Arduino en la débranchant de l’ordinateur et ensuite en la rebranchant. On peut aussi tout simplement appuyer sur le bouton « reset » qui se trouve sur la carte Arduino.

Si on veut programmer un mouvement qui se répète, on doit mettre les blocs de contrôle des servomoteurs et les blocs permettant d’attendre à l’intérieur d’un bloc « Pour toujours » :


Tout ce qui est placé dans ce bloc sera effectué pour toujours. Donc, une fois que les blocs à l’intérieur ont été exécuté, on recommence au début des blocs à l’intérieur. Le tout sera exécuté tant que la carte Arduino est alimentée.

Il n’est pas toujours nécessaire d’avoir un bloc de contrôle pour la position de chaque servomoteur, si, par exemple, un moteur reste à la même position entre deux postures.

3

Défi : créer une danse avec au moins 4 postures différentes et des temps d’attente qui varient entre les 4 postures. On peut mettre plus de postures, bien sûr…

### 4. Utilisation des blocs personnalisés

On remarque assez vite que le code permettant de faire une danse devient très long rapidement et qu’il est parfois difficile de se rappeler l’ordre de chaque posture. En plus, si l’on utilise plusieurs fois la même posture, on répète exactement les mêmes blocs.

Pour faciliter la lecture, la programmation et aussi pour éviter que des sections de code se répètent, on peut utiliser des « blocs personnalisés ». Ceux-ci permettent de regrouper une partie de code et de le réutiliser à plusieurs endroits dans le code.

Par exemple, nous créerons un bloc personnalisé pour la posture des bras en coin.

D’abord, aller dans la partie « Mes blocs » des catégories de blocs.


Cliquer sur « Créer un bloc personnalisé ». La fenêtre suivante s’ouvrira :

4

Écrire « Coin » comme nom du bloc :


Et cliquer ensuite sur « OK ».

Dans la section de code, le bloc suivant est apparu.

Il faut ajouter en-dessous les blocs qui correspondront au bloc « Coin », ici 4 blocs de servomoteurs avec les angles pour réaliser la posture des bras en coin:


On pourra ensuite utiliser un bloc « Coin » en le prenant dans la section « Mes blocs » :


5

Et l’ajouter au programme :


Lors que le code sera exécuté, chaque bloc rose sera remplacé par les blocs qui ont servi à le définir.

La lecture du code sous le bloc « lorsque l’Arduino Uno démarre » sera alors beaucoup plus facile. Aussi, si l’on souhaite changer les angles correspondant à la posture « bras en coin », on peut simplement les changer une fois dans la définition du bloc personnalisé.

Défi : Créer des blocs personnalisés pour chaque posture déjà utilisée précédemment.

On peut aussi créer des blocs qui prennent une valeur en entrée. Par exemple, on pourrait créer un bloc générique appelé « Posture » qui prend 4 valeurs numériques en entrée, appelées Angle1, Angle2, Angle3 et Angle4. On crée d’abord un bloc personnalisé comme précédemment et on écrit « Posture : » comme texte. Ensuite, on cliquer sur « Ajouter une entrée numérique » :


6

On peut ensuite changer « nombre1 » par «Angle1 » :


Et procéder de la même façon pour les 3 autres angles :


Sous le bloc « Définir Posture… », on peut ajouter un bloc de contrôle de servomoteur avec la bonne broche comme ici :


7

On peut ensuite prendre, en cliquant et maintenant avec la sourie, un bloc « Angle1 » dans son emplacement dans le bloc « Définir » :


Et le déplacer jusque dans l’emplacement pour la valeur d’angle dans le premier bloc de servomoteur. On peut procéder de la même façon pour les autres valeurs d’angle :


Dans la catégorie « Mes blocs », le bloc « Posture » a l’air de ceci :


On peut ensuite le prendre et le placer dans le programme et changer la valeur numérique. Par exemple, le code suivant place les bras du Petit Gaillard en haut et ensuite en coin (même chose que le programme de départ) :


8

Défi : Créer un bloc personnalisé « Posture2 » qui prend en entrée 4 valeurs d’angle et un temps d’attente et l’utiliser pour créer une danse.

### 5. Utilisation des blocs « répéter »

Supposons que l’on souhaite répéter une action pour toujours, on peut utiliser le bloc « Pour toujours ». Cependant, il existe d’autres blocs de contrôle qui permettent de répéter une série de blocs pour un nombre de fois prédéterminé où jusqu’à ce qu’une certaine condition soit atteinte.

Regardons d’abord ce bloc-ci :


Ce bloc permet de répéter les blocs qu’il contient le nombre de fois qui est indiqué, ici 10. On peut modifier ce nombre comme on le souhaite.

Ce bloc est très pratique si l’on souhaite, par exemple, refaire 3 fois la même chose. Au lieu de copier 3 fois les mêmes blocs, on peut simplement les mettre à l’intérieur ce celui-ci.

Défi : Utiliser un bloc « Répéter x fois » pour refaire 3 fois le même changement entre 4 postures différentes. Utiliser les blocs personnalisés créés plus haut pour faire les postures.

Le bloc suivant fonctionne un peu de la même façon, mais il permet de répéter une action jusqu’à ce qu’une condition soit vraie :


On peut l’utiliser, ici, pour rendre un mouvement plus graduel ou pour en contrôler le rythme. Jusqu’ici, le passage entre deux postures s’effectue très rapidement. Si l’on

9

souhaite plutôt que le passage d’un bras d’en bas à en haut se fasse en un temps plus long, on ne peut pas simplement passer de la position du bras en haut à en bas directement, car le mouvement se fait tout d’un coup. Il faut plutôt passer par plusieurs valeurs d’angle intermédiaires et mettre un temps d’attente entre chaque valeur.

Par exemple si on veut qu’un moteur passe d’un angle de 0 degré à un angle de 180 degrés en environ 4 secondes, on pourrait lui faire faire des bonds de 10 degrés à chaque 0.25 secondes. En le faisant au long, on obtiendrait quelque chose comme :


Ici, les valeurs ne sont même pas toutes présentes, et on voit déjà que le code sera très long…

En utilisant une variable et un bloc « Répéter », on peut simplifier et accélérer l’écriture. Tout d’abord, créons une variable. Dans la catégorie « Variables », cliquer sur « Créer une variable » :


10

Dans la fenêtre qui apparaît, indiquer le nom de la variable « angle » et cliquer sur « OK » :


Les blocs suivants apparaîtront toujours dans la catégorie « Variables ».

Le premier bloc, « angle » permet d’Avoir accès à la valeur de la variable « angle ».

Le 2e bloc permet de donner une valeur précise à la variable « angle »

Le dernier bloc permet d’ajouter un nombre (ici 1) à la valeur d’angle.


On peut ensuite créer le code suivant qui nous permettra de faire passer le servomoteur branché sur la broche 9 d’une valeur d’agnel de 0 à 180 par bonds de 10 et en attendant 0.25 secondes entre chaque changement.

11


Le bloc suivant :

Est un bloc de type booléen. Cela signifie que sa valeur est « VRAI » ou « FAUX ». Tant que la valeur du bloc est « FAUX », on fait une répétition de plus des blocs situés à l’intérieur du bloc « Répéter ». On sort du bloc « Répéter » lorsque la condition est « VRAI ».

Ainsi, au premier passage,
- angle =0
- Ce qui signifie que « angle » n’est pas supérieur à 180, donc on entre à l’intérieur du bloc « Répéter ».
- Le servomoteur se met à une position de 0 (angle)
- On attend 0.25 s
- On augmente « angle » de 10 : angle =10
- On retourne au début du bloc « Répéter »

Au 2e passage,
- angle =10
- Ce qui signifie que « angle » n’est pas supérieur à 180, donc on entre à l’intérieur du bloc « Répéter ».
- Le servomoteur se met à une position de 10 (angle)
- On attend 0.25 s
- On augmente « angle » de 10 : angle =20
- On retourne au début du bloc « Répéter »

…

12

au 19e passage :
- angle =180
- Ce qui signifie que « angle » n’est pas supérieur à 180, donc on entre à l’intérieur du bloc « Répéter ».
- Le servomoteur se met à une position de 180 (angle)
- On attend 0.25 s
- On augmente « angle » de 10 : angle =190
- On retourne au début du bloc « Répéter »

au 20e passage :
- angle =190
- Ce qui signifie que « angle » est supérieur à 180, donc on sort du bloc « Répéter ».
- On passe aux blocs sous le bloc « Répéter ».

Si l’on fait des bonds de plus grande valeur, le mouvement sera plus saccadé. Même chose si l’on augmente la valeur de temps d’attente entre deux valeurs. En revanche, le mouvement sera plus rapide si le temps d’attente est plus court et si les bonds sont plus grands. Il faut donc trouver la meilleure combinaison entre la rapidité et la fluidité.

Défi : Faire tourner les deux avant-bras en même temps en un mouvement lent et graduel pour passer d’une posture à l’autre comme ceci :

### 6. Défi ultime

Choisir une chanson de votre choix et synchroniser les mouvements du Petit Gaillard avec la musique ! Utiliser les postures choisies ou d’autres, des blocs « Répéter x fois », des blocs « Répéter jusqu’à » et des blocs personnalisés !

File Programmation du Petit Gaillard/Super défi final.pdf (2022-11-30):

### Objectifs :

- Planifier un projet d’IA en classification d’images, de sons ou de postures pour faire bouger le Petit Gaillard
- Entraîner le modèle choisi
- Programmer le Petit Gaillard
- Mettre le tout ensemble pour gagner le plus de points !

### Matériel :

- Kit du Petit Gaillard
- Ordinateur avec webcam et micro et programmes déjà réalisés

### Pointage :

La note finale est sur 100 points répartis comme suit :

- 20 points pour la planification
- Choix du modèle et des classes
- Choix des postures et mouvements pour chaque classe
- Modifications du plan effectuées
- 15 points pour l’efficacité du modèle de reconnaissance
- 10 points pour le nombre de catégories/classe dans le modèle d’IA
- 20 points pour l’efficacité de la programmation du robot
- Présence de postures
- Présence de mouvements souples et de mouvements saccadés
- 15 points sur la qualité du programme
- Présence de commentaires
- Utilisation de blocs de procédures
- 10 points pour l’originalité du projet
- 10 points pour le fonctionnement global

# Super extra défi avec Petit Gaillard!

## Club de robotique

### CÉGEP DE JONQUIÈRE

2

### Planification

Description du projet :

Choix du modèle d’IA :

- Images | Sons | Postures

### Classe # 1 :

Description | | Action du PG

### Classe # 2 :

Description | Action du PG

3

### Classe # 3 :

Description | Action du PG

### Classe # 4 :

Description | Action du PG

### Classe # 5 :

Description | Action du PG

4

### Classe # 6 :

Description | Action du PG

### Classe # 7 :

Description | Action du PG

### Classe # 8 :

Description | Action du PG

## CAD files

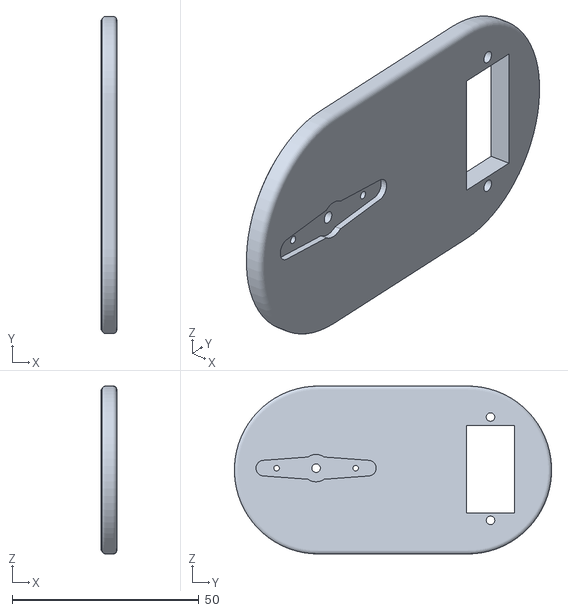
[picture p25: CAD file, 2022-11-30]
Fichiers pour l'impression 3D/Petit Gaillard avant-bras.stl
4.20 x 85.0 x 45.0

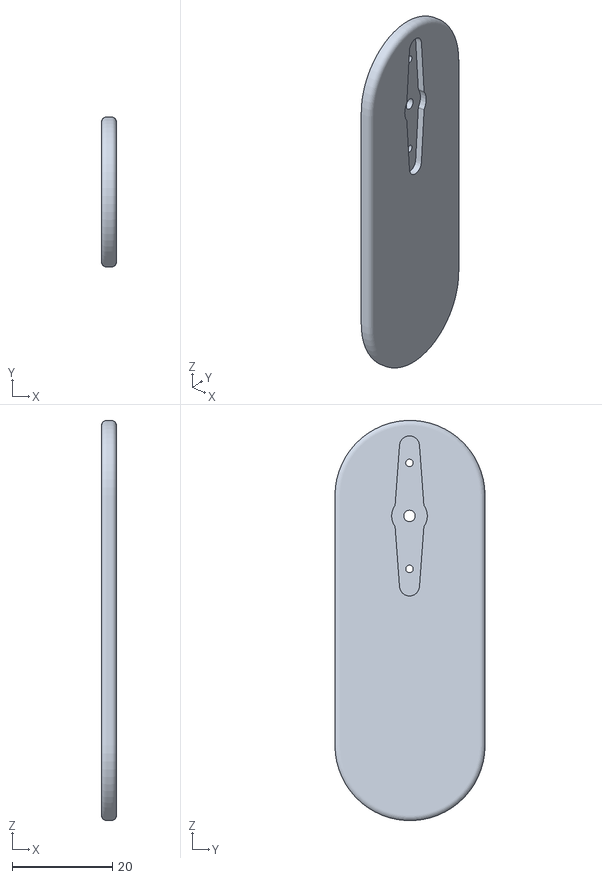
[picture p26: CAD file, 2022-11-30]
Fichiers pour l'impression 3D/Petit Gaillard bras.stl
3.00 x 30.0 x 80.0

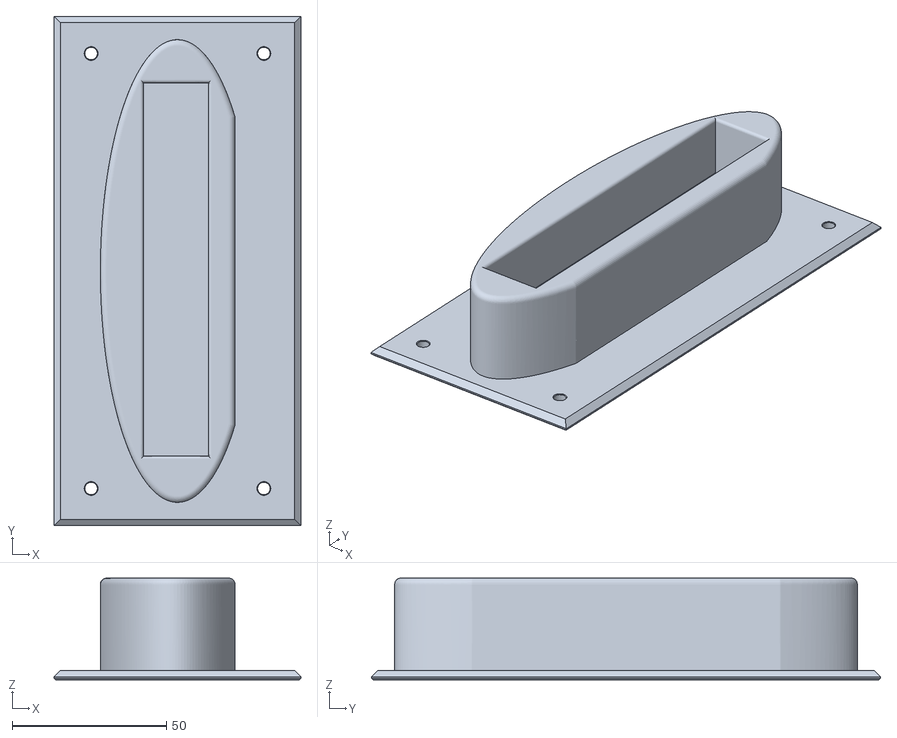
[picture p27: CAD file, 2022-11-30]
Fichiers pour l'impression 3D/Petit Gaillard bas.stl
80.0 x 165.0 x 33.0

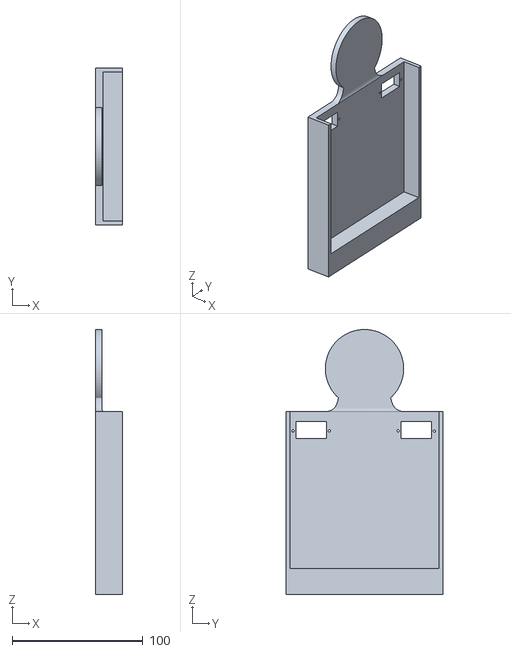
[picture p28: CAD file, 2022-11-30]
Fichiers pour l'impression 3D/Petit Gaillard haut.stl
21.0 x 120.0 x 203.0

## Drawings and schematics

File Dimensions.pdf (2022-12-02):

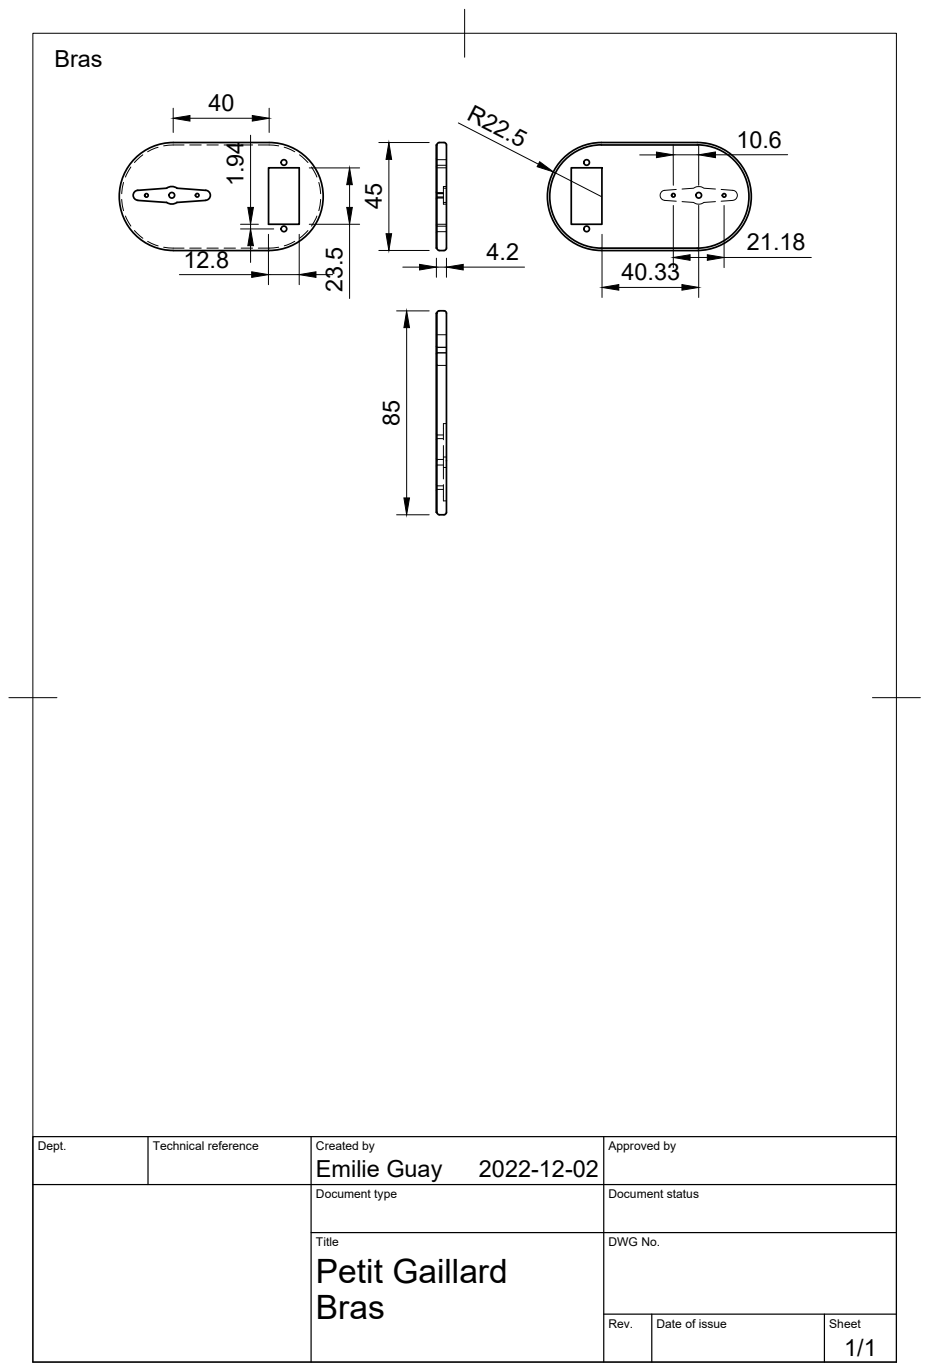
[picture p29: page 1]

Dept. | Technical reference | Created by Emilie Guay 2022-12-02 | Approved by

Document type | Document status

Title Petit Gaillard Bras | DWG No.

Rev. | Date of issue | Sheet

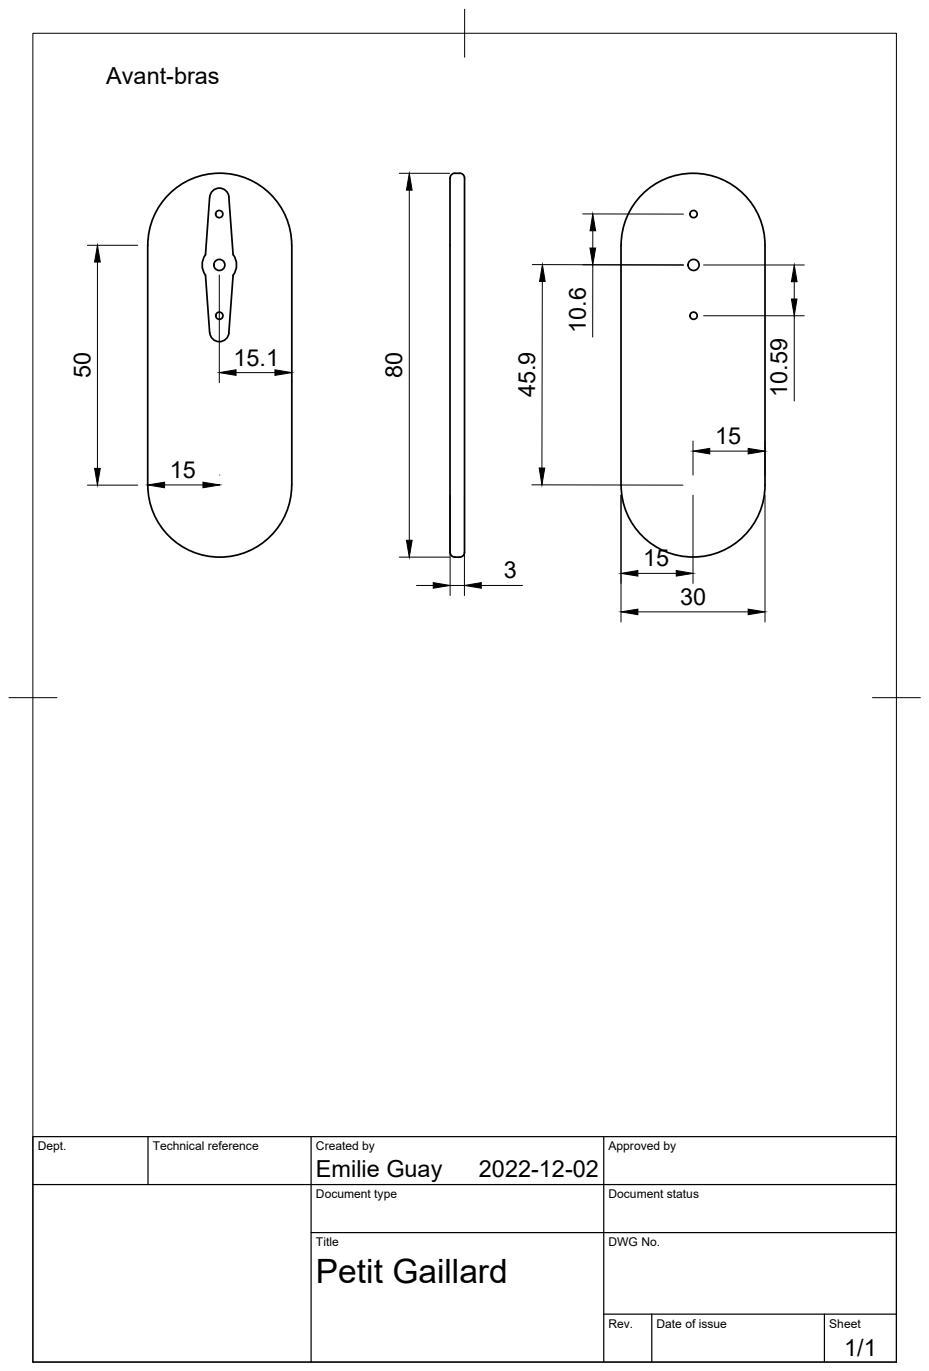
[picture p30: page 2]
Avant-bras 50

Dept. | Technical reference | Created by Emilie Guay 2022-12-02 | Approved by

Document type | Document status

Title Petit Gaillard | DWG No.

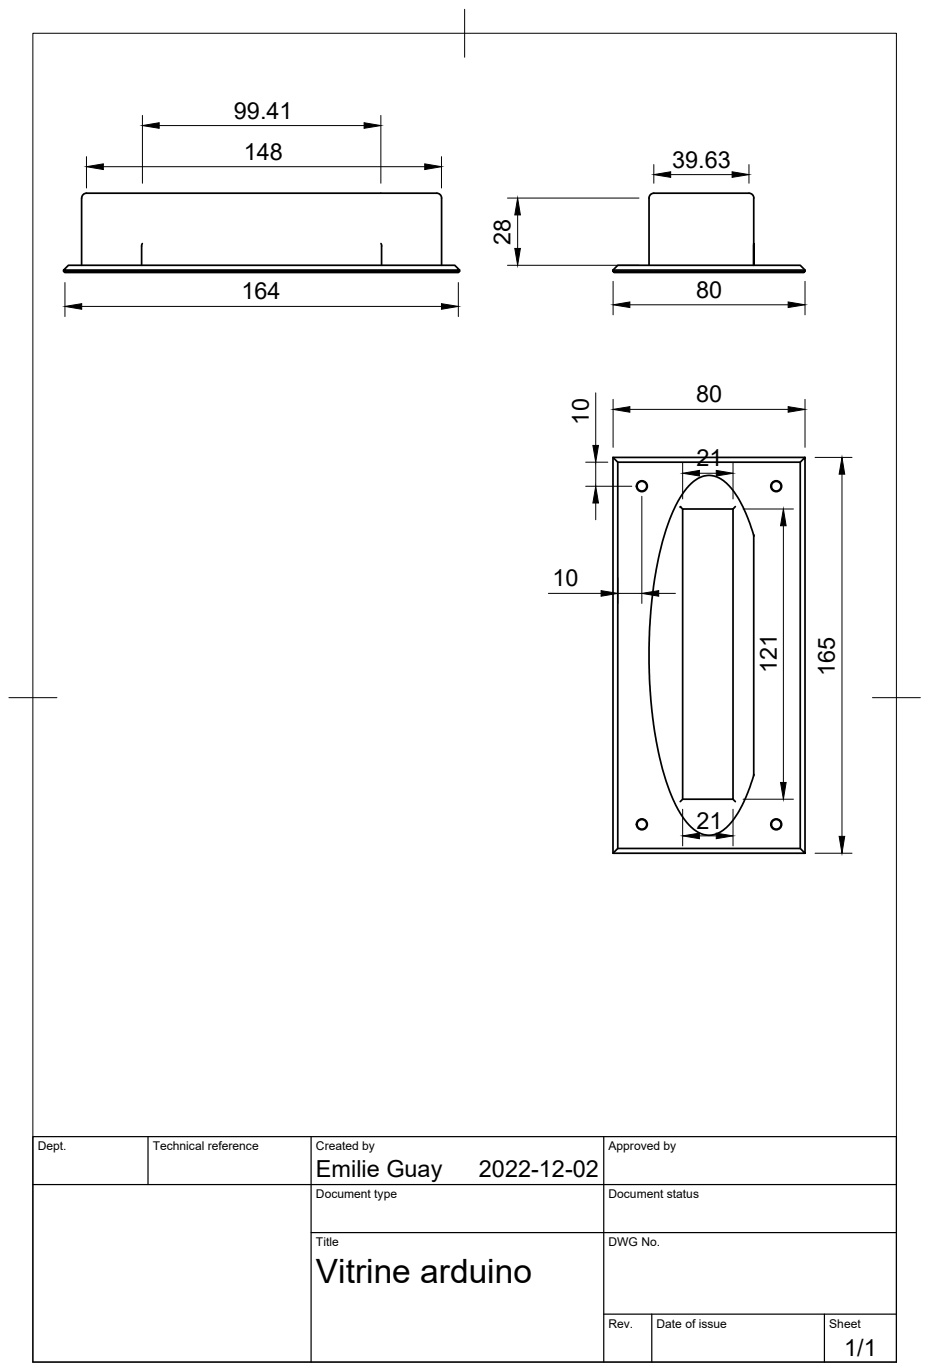
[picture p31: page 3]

Dept. | Technical reference | Created by Emilie Guay 2022-12-02 | Approved by

Document type | Document status

Title Vitrine arduino | DWG No.

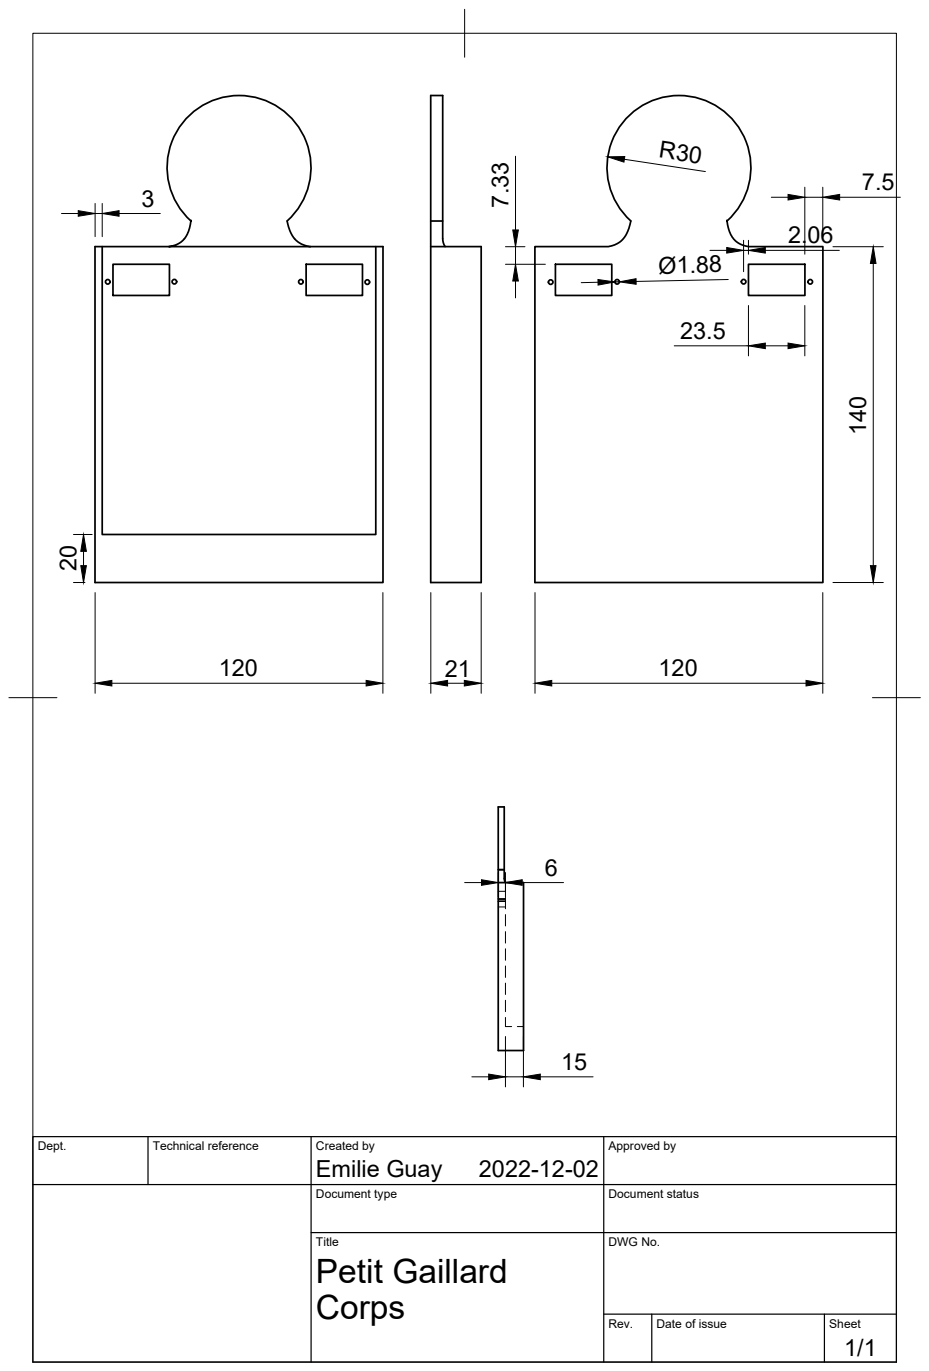
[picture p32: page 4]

Dept. | Technical reference | Created by Emilie Guay 2022-12-02 | Approved by

Document type | Document status

Title Petit Gaillard Corps | DWG No.

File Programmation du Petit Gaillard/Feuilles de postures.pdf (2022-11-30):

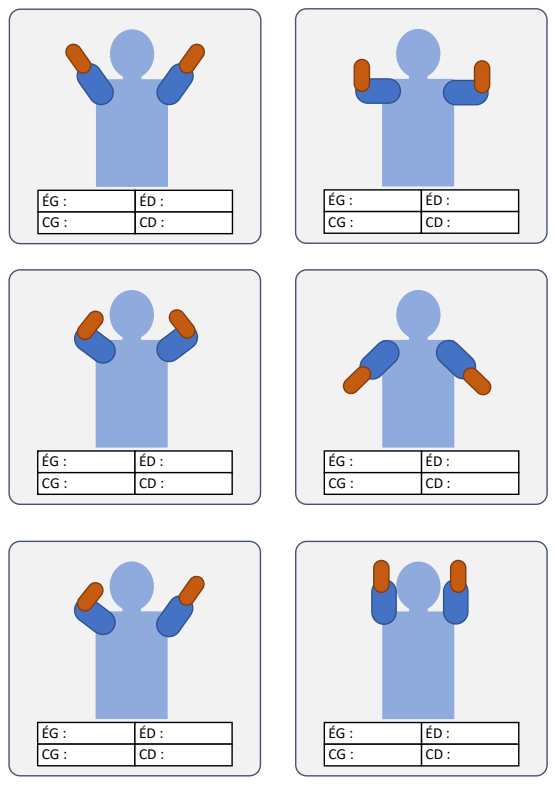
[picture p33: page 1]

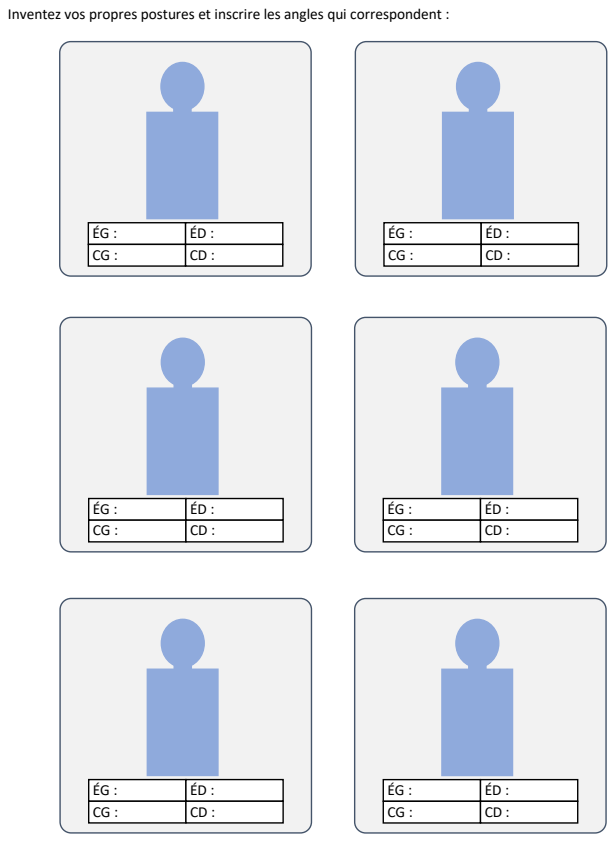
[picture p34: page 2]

Inventez vos propres postures et inscrire les angles qui correspondent :

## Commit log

2022-11-30 Ajout des fichiers pour l'impression 3D
    [Petit Gaillard avant-bras.stl, Petit Gaillard bas.stl, Petit Gaillard bras.stl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]
2022-11-30 Ajout des fichiers de programmation
2022-12-01 Ajout du fichier de matériel et préparation
2022-12-02 Ajout du fichiers de quotations
2022-12-05 Ajout des fichiers pour une activité avec le PG
